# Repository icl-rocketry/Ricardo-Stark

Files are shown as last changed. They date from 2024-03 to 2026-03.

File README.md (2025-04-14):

# Ricardo-Stark (Engine Control Unit)

An integrated engine control unit designed to fire and control liquid bi-propellant rocket engines. Stark v1.0 has been tested in several cold flows and hotfire tests for engines ranging from 500N to 5kN. It has been flight tested on Nimbus 24 (ICLR's first liquid rocket launch) at the European Rocketry Challenge '24.

## Hardware (v1.0)
- ESP32-S3 microcontroller
- x2 Servo Channels with voltage monitor
- x1 Pyro Channel with regulated 12V
- x6 24 bit ADC channels
- microSD card logging
- x4 GPIO breakout
- CAN Bus
- USB-C Port

## Software (v1.0)
- Finite State Machine implementation
- Custom ignition sequence with propellant feed delay
- Custom valve angle configuration
- Optional remote configurability to ignition sequence

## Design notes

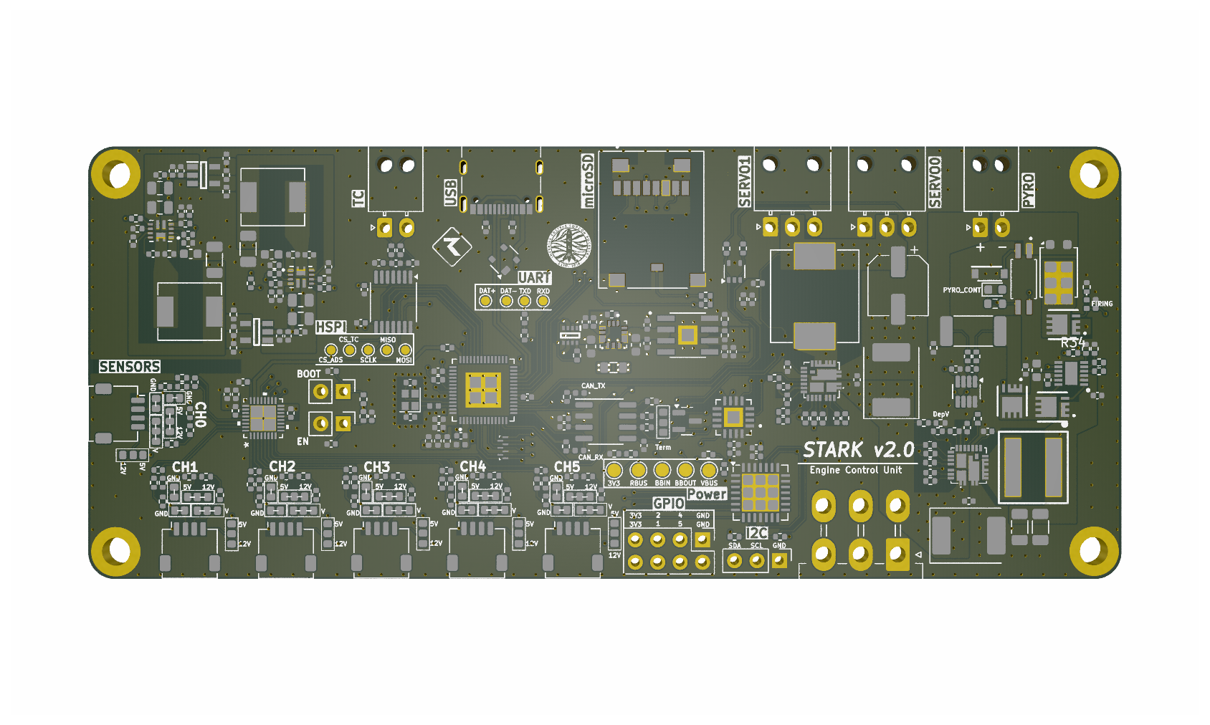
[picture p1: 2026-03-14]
Hardware/Ricardo-Stark.png

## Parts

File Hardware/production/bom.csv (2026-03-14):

Designator | Footprint | Quantity | Value | LCSC Part #
12VLED1, 3V3LED6 | 0402 | 2 | RED_LED
3V3LED1, 3V3LED4, 3V3LED8 | 0402 | 3 | BLUE_LED
3V3LED10 | 0402 | 1 | PURPLE_LED
3V3LED5 | 0402 | 1 | ORANGE_LED
3V3LED7 | 0402 | 1 | YELLOW_LED
BOOTJUMPER1, ENJUMPER1 | PinHeader_1x02_P2.54mm_Vertical | 2 | Conn_01x02_Male
C1, C15, C17, C21, C23, C31, C36, C58, C68 | 0402 | 9 | 10uF
C10, C11, C24, C3, C30, C35, C45, C5, C6, C71, C72, C76, C77, C8, C80, C84, C86, C87, C88, C89 | 0402 | 20 | 0.1uF
C12, C13 | 0402 | 2 | 11pF
C14, C32, C34, C54, C56, C59, C66, C67, C69, C83, C90 | 0402 | 11 | 100nF
C16 | 0402 | 1 | 47nF
C18, C61 | 0603 | 2 | 10uF
C19, C2, C25, C37, C4, C51, C60, C7, C73, C82 | 0402 | 10 | 1uF
C20 | 0603 | 1 | 22uF
C22, C26, C74 | 0402 | 3 | 4.7uF
C27, C28 | CP_EIA-7360-38_Kemet-E | 2 | 100uF
C29 | CP_Elec_6.3x7.7 | 1 | 470uF
C33, C38, C41, C42, C43, C44, C9 | 0402 | 7 | 10nF
C39, C52, C53, C64 | 0805 | 4 | 22uF
C40, C57, C75 | 1206 | 3 | 47uF
C46 | 0402 | 1 | 1uF | GRT188R61H225KE13D
C47 | 0603 | 1 | 0.1uF
C48 | 0603 | 1 | 2.2uF
C49 | 0402 | 1 | 180pF
C50 | 0402 | 1 | 3.9nF
C55, C65 | 0402 | 2 | 2.2uF
C62 | 0402 | 1 | 120pF
C63 | 0402 | 1 | 2.2nF
C70 | 1206 | 1 | 22uF
C78 | 0603 | 1 | 160pF
C79, C85 | 0402 | 2 | 0.01uF
C81 | 0402 | 1 | 220nF
CANRXLED1 | 0402 | 1 | CANRXLED
CANTXLED1 | 0402 | 1 | CANTXLED
D1 | SOT-23 | 1 | SM712_SOT23
D2 | SOT-143 | 1 | SP0503BAHT
D3 | TO-277B | 1 | DST1550S
D4 | 0603 | 1 | RED_LED
D6 | SOT-353_SC-70-5 | 1 | ~
D7 | RCLAMP3346PQTNT | 1 | RCLAMP3346PQTNT
D9 | SODFL3516X70N | 1 | S-102T
FIRING1 | 0402 | 1 | EMERALD_LED
H1, H2, H3, H4 | MountingHole_3.2mm_M3_DIN965_Pad | 4 | MountingHole_Pad
IC1, IC4 | IC_TPS61089RNRR | 2 | TPS61089RNRR
IC2, IC3 | SOT95P282X145-5N | 2 | AP2205-W5-7
J1 | Molex_Mini-Fit_Jr_5569-06A2_2x03_P4.20mm_Horizontal | 1 | RBUS
J10, J4, J6, J7, J8, J9 | Molex_Pico-Clasp_202396-0407_1x04-1MP_P1.00mm_Horizontal | 6 | 1053131104
J11 | PinHeader_2x04_P2.54mm_Vertical | 1 | Conn_01x08_Socket
J12 | Molex_Nano-Fit_105313-xx02_1x02_P2.50mm_Horizontal | 1 | Conn_01x02_Male
J16 | Molex_Pico-Clasp_202396-0707_1x07-1MP_P1.00mm_Horizontal | 1 | Conn_01x07_Socket
J17 | Molex_Nano-Fit_105313-xx03_1x03_P2.50mm_Horizontal | 1 | ServoCH1
J18 | Molex_Nano-Fit_105313-xx03_1x03_P2.50mm_Horizontal | 1 | ServoCH2
J2 | USB_C_Receptacle_Palconn_UTC16-G | 1 | USB_C_Receptacle_USB2.0
J3 | JAE_ST1W008S4TR2000 | 1 | ST1W008S4TR2000
J5 | PinHeader_1x03_P2.54mm_Vertical | 1 | Conn_01x03_Socket
JP10, JP12, JP13, JP14, JP17, JP18, JP19, JP20, JP23, JP24, JP25, JP28, JP29, JP3, JP30, JP33, JP5, JP6, JP7 | small_3pin_SolderJP | 19 | SolderJumper_3_Open
JP11, JP15, JP16, JP21, JP22, JP26, JP27, JP31, JP32, JP4, JP8, JP9 | SmallerSolderJP | 12 | SolderJumper_2_Open
L1 | 0402 | 1 | 2.0nH
L2 | 0402 | 1 | 20nH
L3 | 0805 | 1 | 1uH
L4 | IND_SPM10065VT-3R3M-D | 1 | 3.3uH
L5, L6 | IND_SRP6540-390M | 2 | SRR6038-5R0Y
L7 | WE-XHMI_7070 | 1 | 3.3uH
Q5, Q6, Q7 | BSZ025N04LS | 3 | BSZ025N04LS
R1, R10, R101, R13, R14, R21, R24, R25, R27, R30, R33, R38, R5, R50, R56, R76, R81, R83, R88, R9, R95 | 0402 | 21 | 10K
R100, R22, R37, R48, R55, R75, R92 | 0402 | 7 | 14k
R102, R103, R2, R3, R39, R40, R46, R47, R51, R52, R57, R58, R96, R97 | 0402 | 14 | 1k
R104, R41, R49, R53, R59, R98 | 0402 | 6 | 49
R105, R106 | 0402 | 2 | 2.2k
R107 | 0402 | 1 | 432k
R109, R110 | 0402 | 2 | 165R
R11, R94 | 0402 | 2 | 4.7k
R111, R112 | 0402 | 2 | 100
R12, R4, R43, R6 | 0402 | 4 | 470
R15 | 0402 | 1 | 0
R16, R17 | 0402 | 2 | 60.4
R18, R19, R20, R71 | 0402 | 4 | 5.1k
R23 | 0402 | 1 | 56k
R26 | 0402 | 1 | 130k
R28, R84 | 0402 | 2 | 2.2
R29 | 0402 | 1 | 294k
R31 | 0402 | 1 | 499k
R32, R44, R62, R69, R87 | 0402 | 5 | 100k
R36, R45, R54, R74, R78, R99 | 0402 | 6 | 75k
R42 | 0402 | 1 | 1.5k
R60 | 0402 | 1 | 7.87k
R61 | 0402 | 1 | 360k
R63 | 0402 | 1 | 560k
R64, R70 | 0402 | 2 | 49.9k
R65 | 0402 | 1 | 150k
R66 | 0402 | 1 | 301k
R67 | 0402 | 1 | 18.7k
R68 | 0402 | 1 | 976k
R7 | 0402 | 1 | 499R
R72 | 0402 | 1 | 475k
R73 | 0402 | 1 | 287k
R77 | 0402 | 1 | 120
R79 | 0603 | 1 | 120
R8 | 0402 | 1 | 3k
R80 | 0402 | 1 | 4.22k
R82 | 0402 | 1 | 190k
R85 | 2512 | 1 | 2m | WSLF25122L000FEB
R86 | 0402 | 1 | 200k
R89, R93 | 0402 | 2 | 10
R90 | 0603 | 1 | 5.1
R91 | 0402 | 1 | 54.9R
TC1 | Molex_Nano-Fit_105313-xx02_1x02_P2.50mm_Horizontal | 1 | Thermocouple
TP1, TP13, TP14, TP15, TP16, TP17, TP2, TP3, TP4 | TestPoint_Pad_D1.0mm | 9 | TestPoint
TP11, TP5, TP6, TP7, TP8 | TestPoint_Pad_D1.5mm | 5 | TestPoint
TXLED1 | 0402 | 1 | GREEN_LED
U1 | QFN40P700X700X90-57N | 1 | ESP32-S3
U10 | SiC437BEDT1GE3 | 1 | SiC438BED-T1-GE3
U11 | SON50P300X300X80-13N-D | 1 | LM74810
U12 | SOT-23-8 | 1 | INA219AxDCN
U13 | TSSOP-14_4.4x5mm_P0.65mm | 1 | MAX31856
U14 | QFN65P400X400X100-17N | 1 | PCA9534RGVR
U2 | SOIC-8_3.9x4.9mm_P1.27mm | 1 | SN65HVD230
U3 | SOTFL50P160X60-8N | 1 | LM66200DRLR
U4 | CONV_MAX77827AEFD+T | 1 | MAX77827AEFD+T
U5 | SOIC127P599X175-9N | 1 | SC4215
U6 | SiC437BEDT1GE3 | 1 | SiC437BED-T1-GE3
U7 | ADS131M06IRSNR | 1 | ADS131M06IPBS
U8 | QFN-28-1EP_6x6mm_P0.65mm_EP4.25x4.25mm | 1 | PCA9685BS
U9 | TCMT1109-4N | 1 | 782-TCMT1109
USBLED1 | 0402 | 1 | WHITE_LED
Y1 | Crystal_SMD_2016-4Pin_2.0x1.6mm | 1 | R940000171

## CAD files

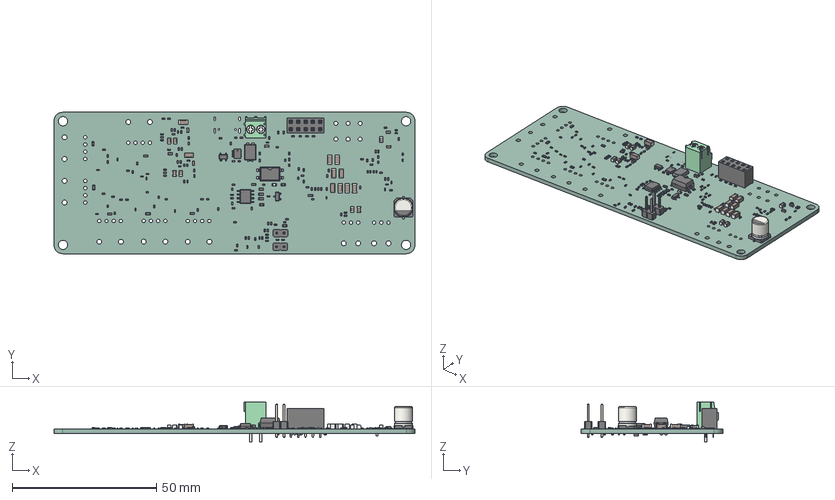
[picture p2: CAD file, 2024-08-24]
Hardware/Ricardo-Stark.step
125.0 x 49.0 x 13.7 mm
R_0402_1005Metric x 95
LED_0402_1005Metric x 12
R_0603_1608Metric x 16
C_0805_2012Metric x 6
C_0603_1608Metric x 6
C_0402_1005Metric x 54
SOIC_8_39x49mm_P127mm
L_0402_1005Metric x 2
PinHeader_1x02_P254mm_Vertical x 2
C_1206_3216Metric x 10
SMDIP_4_W953mm
TerminalBlock_Phoenix_PT_15_2_35_H_1x02_P350mm_Horizontal
SOT_143
TO_277B_sp
SOT-1210_LFPAK33
PinSocket_2x05_P254mm_Vertical
SOT_23
LED_0603_1608Metric
L_0805_2012Metric
CP_Elec_63x77
Ricardo-Stark_PCB

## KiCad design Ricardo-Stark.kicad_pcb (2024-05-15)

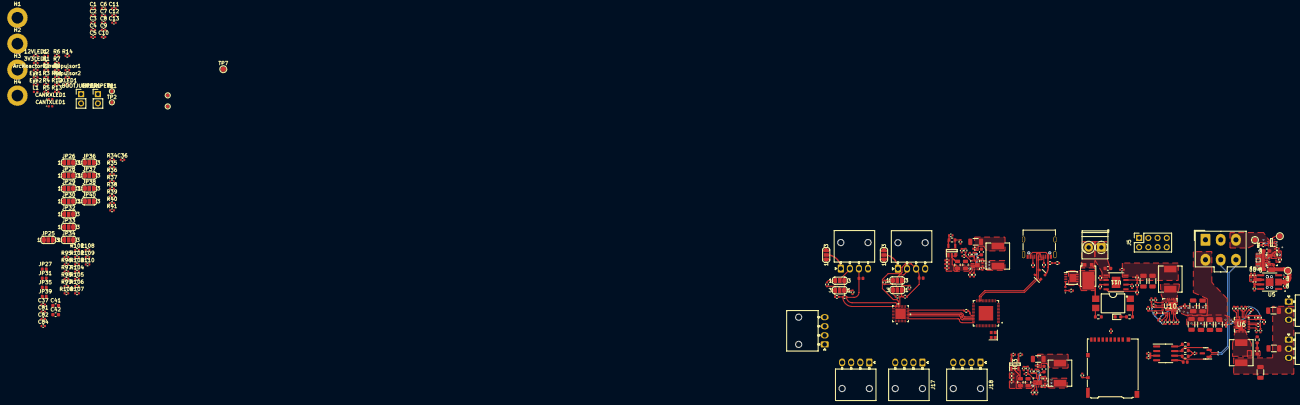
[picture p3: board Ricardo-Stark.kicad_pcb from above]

Board: 4 copper layers, 265 parts (0 on the bottom side), 164 nets.

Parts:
3V3LED1: BLUE_LED; R_0402_1005Metric
12VLED1: RED_LED; R_0402_1005Metric
ArcReactorCore1: Blue_LED; R_0402_1005Metric
BOOTJUMPER1: Conn_01x02_Male; PinHeader_1x02_P2.54mm_Vertical
C1, C15, C17, C21, C23, C58, C68: 10uF; C_0402_1005Metric
C2, C4, C7, C19, C25, C37, C51, C60, C73, C82: 1uF; C_0402_1005Metric
C3, C5, C6, C8, C10, C11, C24, C35, C36, C76, C77, C84: 0.1uF; C_0402_1005Metric
C9: 10nF; C_0402_1005Metric
C12, C13: 11pF; C_0402_1005Metric
C14, C34, C54, C56, C59, C66, C67, C69, C83, C86: 100nF; C_0402_1005Metric
C16: 47nF; C_0402_1005Metric
C18, C41, C61: 10uF; C_0603_1608Metric
C20: 22uF; C_0603_1608Metric
C22, C26, C74: 4.7uF; C_0402_1005Metric
C27, C28, C40, C57, C75, C80, C85: 47uF; C_1206_3216Metric
C29: 68uF; C_1206_3216Metric
C30, C32: DNP; C_1206_3216Metric
C31, C33: 220uF; C_1206_3216Metric
C39, C52, C53, C64: 22uF; C_0805_2012Metric
C42: 100nF; C_0603_1608Metric
C48: 2.2uF; C_0603_1608Metric
C49: 180pF; C_0402_1005Metric
C50: 3.9nF; C_0402_1005Metric
C55, C65: 2.2uF; C_0402_1005Metric
C62: 120pF; C_0402_1005Metric
C63, C87: 2.2nF; C_0402_1005Metric
C70: 22uF; C_1206_3216Metric
C78: 680pF; C_0603_1608Metric
C81: 220nF; C_0402_1005Metric
C88: 1uF; C_0603_1608Metric
CANRXLED1: CANRXLED; LED_0402_1005Metric
CANTXLED1: CANTXLED; LED_0402_1005Metric
D1: SM712_SOT23; SOT-23
D2: SP0503BAHT; SOT-143
D3: DST1550S; TO-277B
D4: RED_LED; LED_0603_1608Metric
ENJUMPER1: Conn_01x02_Male; PinHeader_1x02_P2.54mm_Vertical
Eye1, Eye2: Blue_LED; R_0402_1005Metric
Firing1: EMERALD_LED; LED_0402_1005Metric
H1, H2, H3, H4: MountingHole_Pad; MountingHole_3.2mm_M3_DIN965_Pad
IC1, IC4: TPS61089RNRR; IC_TPS61089RNRR
IC2, IC3: AP2205-W5-7; SOT95P282X145-5N
J1: RBUS; Molex_Mini-Fit_Jr_5566-06A_2x03_P4.20mm_Vertical
J2: USB_C_Receptacle_USB2.0; USB_C_Receptacle_Palconn_UTC16-G
J3: ServoCH1; Molex_Nano-Fit_105313-xx03_1x03_P2.50mm_Horizontal
J4: ServoCH2; Molex_Nano-Fit_105313-xx03_1x03_P2.50mm_Horizontal
J5: GPIO Breakout; PinSocket_2x04_P2.54mm_Vertical
J7, J14, J15, J16, J17, J18: 1053131104; Molex_Nano-Fit_105313-xx04_1x04_P2.50mm_Horizontal
J12: Conn_01x02_Male; TerminalBlock_Phoenix_PT-1,5-2-3.5-H_1x02_P3.50mm_Horizontal
J13: Micro_SD_Card_Det; microSD_HC_Hirose_DM3AT-SF-PEJM5
JP1: TermJP; SmallerSolderJP
JP5, JP10, JP20, JP21, JP22, JP24, JP25, JP26, JP28, JP29, JP30, JP32, JP33, JP34, JP36, JP37, JP38, JP40: SolderJumper_3_Open; SolderJumper-3_P1.3mm_Open_RoundedPad1.0x1.5mm_NumberLabels
JP8, JP23, JP27, JP31, JP35, JP39: SolderJumper_2_Open; SmallerSolderJP
L1: 2.0nH; L_0402_1005Metric
L2: 20nH; L_0402_1005Metric
L3: 1uH; L_0805_2012Metric
L4, L7: 3.3uH; IND_SRP6540-390M
L5, L6: SRR6038-5R0Y; IND_SRP6540-390M
Q2: BUK9M11-40EX; LFPAK33
R1, R5, R9, R10: 10K; R_0402_1005Metric
R2, R3, R11, R12, R13: 1k; R_0402_1005Metric
R4, R6, R35: 470; R_0402_1005Metric
R7: 499R; R_0402_1005Metric
R8, R14: 3k; R_0402_1005Metric
R15: 0; R_0603_1608Metric
R16, R17: 60; R_0603_1608Metric
R18, R19, R20: 5.1k; R_0402_1005Metric
R21, R24, R25, R27, R33, R48, R76, R81, R83, R88, R89, R96, R100, R104, R108: 10k; R_0402_1005Metric
R22: 14k; R_0402_1005Metric
R23: 56k; R_0402_1005Metric
R26: 130k; R_0402_1005Metric
R28, R84: 2.2; R_0402_1005Metric
R29: 294k; R_0402_1005Metric
R30: 464K; R_0402_1005Metric
R31, R86: 200k; R_0402_1005Metric
R32, R62, R69, R87: 100k; R_0402_1005Metric
R34: 1.5k; R_0402_1005Metric
R36, R37, R38, R39, R40, R41: DNP; R_0402_1005Metric
R45, R75, R95, R99, R103, R107: 58.4k; R_0402_1005Metric
R51, R92, R98, R102, R106, R110: 49; R_0402_1005Metric
R60: 7.87k; R_0402_1005Metric
R61: 360k; R_0402_1005Metric
R63: 560k; R_0402_1005Metric
R64: 50k; R_0402_1005Metric
R65: 152k; R_0603_1608Metric
R66: 301k; R_0402_1005Metric
R67: 18.7k; R_0402_1005Metric
R68: 900k; R_0402_1005Metric
R70: 51k; R_0402_1005Metric
R71: 33.2k; R_0402_1005Metric
R72: 475k; R_0402_1005Metric
R73: 287k; R_0402_1005Metric
R74, R78, R97, R101, R105, R109: 31.6k; R_0402_1005Metric
R77: 120; R_0402_1005Metric
R79: 120; R_0603_1608Metric
R80: 10k; R_0603_1608Metric
R82: 190k; R_0402_1005Metric
R85: 47.5k; R_0402_1005Metric
R90: 5.1; R_0603_1608Metric
R91: 54.9R; R_0402_1005Metric
R93: 453; R_0402_1005Metric
R94: 11.52; R_0402_1005Metric
Repulsor1, Repulsor2: White_LED; R_0402_1005Metric
TP1, TP2, TP3, TP4: TestPoint; TestPoint_Pad_D1.0mm
TP5, TP6, TP7, TP8: TestPoint; TestPoint_Pad_D1.5mm
TXLED1: GREEN_LED; R_0402_1005Metric
U1: ESP32-S3; QFN40P700X700X90-57N
U2: SN65HVD230; SOIC-8_3.9x4.9mm_P1.27mm
U3: LM66200DRLR; SOTFL50P160X60-8N
U4: MAX77827AEFD+T; CONV_MAX77827AEFD+T
U5: SC4215; SOIC127P599X175-9N
U6, U10: SiC437BED-T1-GE3; SiC437BEDT1GE3
U7: ADS131M06IPBS; ADS131M06IRSNR
U9: 859-LTV-247; SMDIP-4_W9.53mm
U11: TPS259621DDAT; SO-PP-DDA-8_TEX
USBLED1: WHITE_LED; R_0402_1005Metric
Y1: R940000171; Crystal_SMD_2016-4Pin_2.0x1.6mm

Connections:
+3.3V: C1.1, C4.1, C5.1, C7.1, C9.1, C10.1, C11.1, C14.1, C15.1, C23.2, C24.2, C37.1, C41.1, C42.1, C56.1, C57.1, C67.1, C70.1, C77.1, C82.1, C84.1, IC1.9 (VIN), IC4.9 (VIN), J5.5, J13.4 (VDD), L1.1, L5.1, L6.1, R1.1, R2.1, R3.1, R4.1, R5.1, R6.2, R9.2, R10.2, R11.1, R12.1, R13.1, R14.1, R23.1, R36.1, R37.1, R38.1, R39.1, R40.1, R41.1, R89.1, R94.2, TP7.1, U1.20 (VDD3P3_RTC), U1.46 (VDD3P3_CPU), U1.55 (VDDA), U1.56 (VDDA), U2.3 (VCC), U5.6 (VOUT), U7.15 (AVDD), U7.16 (SYNC/RESET), U7.26 (DVDD), U9.16
+5V: C55.1, IC2.5 (VOUT), JP10.1 (A), JP24.1 (A), JP28.1 (A), JP32.1 (A), JP36.1 (A), JP40.1 (A), R65.2
+6V: C29.1, C31.1, C33.1, C36.1, J3.2, J4.2, L4.1, R26.2, R29.2, R34.2, U6.18 (V_OUT)
+12V: C65.1, IC3.5 (VOUT), JP10.3 (B), JP24.3 (B), JP28.3 (B), JP32.3 (B), JP36.3 (B), JP40.3 (B)
/ADS_CLK: R91.1, U7.23 (XTAL1/CLKIN)
/ADS_CS0: U1.42 (GPIO37), U7.17 (CS)
/BOOT: BOOTJUMPER1.1, C8.1, R5.2, U1.5 (GPIO0/BOOT)
/Boosts/FB_5V: IC1.3 (FB), R61.1, R62.2
/Boosts/FB_12V: IC4.3 (FB), R68.1, R69.2
/Boosts/LDO5.5V_IN: C51.1, C52.1, C53.1, C58.1, C59.1, IC1.6 (VOUT), IC2.1 (VIN), IC2.3 (EN), R61.2
/Boosts/LDO12V_IN: C39.1, C60.1, C64.1, C68.1, C69.1, IC3.1 (VIN), IC3.3 (EN), IC4.6 (VOUT), R68.2
/Boosts/SW_5V: IC1.1 (FSW), R66.1
/Boosts/SW_12V: IC4.1 (FSW), R73.1
/CAN+: D1.2 (A2), J1.5, R16.1, U2.7 (CANH)
/CAN-: D1.1 (A1), J1.6, R17.2, U2.6 (CANL)
/CAN-BUS/Vref: JP1.1 (A), U2.5 (Vref)
/CAN_RX: CANRXLED1.1 (K), U1.6 (GPIO1/ADC1_CH0), U2.4 (R)
/CAN_TX: CANTXLED1.1 (K), U1.7 (GPIO2/ADC1_CH1), U2.1 (D)
/CHIP_PU: C2.1, C3.1, ENJUMPER1.1, R1.2, U1.4 (CHIP_PU/RESET)
/Cont 1: R79.1, U1.28 (SPI_CS1/GPIO26), U9.15
/Data+: D2.4 (K), J2.A6 (D+), J2.B6 (D+), TP4.1, U1.26 (GPIO20/USB_D+/ADC2_CH9)
/Data-: D2.3 (K), J2.A7 (D-), J2.B7 (D-), TP3.1, U1.25 (GPIO19/USB_D-/ADC2_CH8)
/HSPI_MISO: U1.39 (GPIO34), U7.20 (DOUT)
/HSPI_MOSI: U1.38 (GPIO33), U7.21 (DIN)
/HSPI_SCLK: U1.40 (GPIO35), U7.19 (SCLK)
/Nuke 1: Firing1.2 (A), Q2.4 (G), U1.27 (GPIO21)
/Power/BBIN: C17.1, C18.1, TP5.1, U3.2 (VOUT_1), U3.7 (VOUT_2), U4.3 (EN), U4.6 (IN)
/Power/BBOUT: C20.1, C21.1, C22.1, TP8.1, U4.11 (OUT), U4.13 (OUTS), U5.2 (EN), U5.3 (VIN)
/Power/BIAS: C19.1, U4.5 (BIAS)
/Power/FBIn: R23.2, R24.1, U5.7 (ADJ)
/Power/LX1: L3.1, U4.8 (LX1)
/Power/LX2: L3.2, U4.10 (LX2)
/Power/SEL: R22.1, U4.1 (SEL)
/Pyro/BOOT: C76.1, U10.23 (BOOT)
/Pyro/EFuse_In: C40.1, C75.1, C86.1, L7.1, R30.2, R82.2, U10.18 (V_OUT), U11.4 (IN)
/Pyro/EN: R88.1, U10.19 (EN)
/Pyro/FB: R82.1, R83.2, U10.17 (FB)
/Pyro/PHASE: R84.1, U10.24 (PHASE)
/Pyro/PyroV: C88.2, J12.1, U11.5 (OUT)
/Pyro/SW: L7.2, U10.5 (SW_1), U10.6 (SW_2), U10.7 (SW_3), U10.8 (SW_4), U10.9 (SW_5), U10.30 (SW_6)
/Pyro/VDD: C73.2, R81.1, R86.2, U10.15 (VDD)
/Pyro_IMON: R93.1, U1.24 (GPIO18/ADC2_CH7/DAC_1), U11.7 (ILM)
/RXD: TP2.1, U1.50 (U0RXD/PROG/GPIO44)
/SD1_DET: J13.10 (DET_A), R89.2, U1.23 (GPIO17/ADC2_CH6/DAC_2)
/Servo1PWM: J3.3, U1.16 (GPIO11/ADC2_CH0)
/Servo2PWM: J4.3, U1.15 (GPIO10/ADC1_CH9)
/ServoV_LOG: C36.2, R34.1, R35.2, U1.18 (GPIO13/ADC2_CH2)
/TXD: R7.1, TP1.1, TXLED1.1 (K)
/actuators/GPIO0: J5.2, R36.2
/actuators/GPIO1: J5.3, R37.2
/actuators/GPIO2: J5.4, R38.2
/actuators/GPIO3: J5.6, R39.2
/actuators/GPIO4: J5.7, R40.2
/actuators/GPIO5: J5.8, R41.2
/buckC/BOOT: C35.1, U6.23 (BOOT)
/buckC/EN: R33.1, U6.19 (EN)
/buckC/FB: R26.1, R27.2, R29.1, U6.17 (FB)
/buckC/PHASE: R28.1, U6.24 (PHASE)
/buckC/SW: C78.1, L4.2, U6.5 (SW_1), U6.6 (SW_2), U6.7 (SW_3), U6.8 (SW_4), U6.9 (SW_5), U6.30 (SW_6)
/buckC/VDD: C25.2, R25.1, R31.2, U6.15 (VDD)
/pressure_sensor/AIN0N: J7.3, JP8.2 (B), R51.2, U7.30 (AIM0N)
/pressure_sensor/AIN0P: JP5.3 (B), JP20.1 (A), R51.1, R75.2, R76.2, U7.29 (AIN0P)
/pressure_sensor/AIN1N: J14.3, JP23.2 (B), R92.2, U7.31 (AIN1N)
/pressure_sensor/AIN1P: JP21.3 (B), JP22.1 (A), R45.2, R48.2, R92.1, U7.32 (AIN1P)
/pressure_sensor/AIN2N: J15.3, JP27.2 (B), R98.2, U7.2 (AIN2N)
/pressure_sensor/AIN2P: JP25.3 (B), JP26.1 (A), R95.2, R96.2, R98.1, U7.1 (AIN2P)
/pressure_sensor/AIN3N: J16.3, JP31.2 (B), R102.2, U7.3 (AIN3N)
/pressure_sensor/AIN3P: JP29.3 (B), JP30.1 (A), R99.2, R100.2, R102.1, U7.4 (AIN3P)
/pressure_sensor/AIN4N: J17.3, JP35.2 (B), R106.2, U7.6 (AIN4N)
/pressure_sensor/AIN4P: JP33.3 (B), JP34.1 (A), R103.2, R104.2, R106.1, U7.5 (AIN4P)
/pressure_sensor/AIN5N: J18.3, JP39.2 (B), R110.2, U7.7 (AIN5N)
/pressure_sensor/AIN5P: JP37.3 (B), JP38.1 (A), R107.2, R108.2, R110.1, U7.8 (AIN5P)
DeployV: C27.1, C28.1, C30.1, C32.1, C34.1, C80.1, C83.1, C85.1, J1.4, R8.1, R33.2, R88.2, U6.1 (V_IN_1), U6.2 (V_IN_2), U6.22 (VIN_1), U6.26 (VIN_2), U10.1 (V_IN_1), U10.2 (V_IN_2), U10.22 (VIN_1), U10.26 (VIN_2)
GND: 3V3LED1.1 (K), 12VLED1.1 (K), ArcReactorCore1.1 (K), BOOTJUMPER1.2, C1.2, C2.2, C3.2, C4.2, C5.2, C6.2, C7.2, C8.2, C9.2, C10.2, C11.2, C12.2, C13.2, C14.2, C15.2, C16.2, C17.2, C18.2, C19.2, C20.2, C21.2, C22.2, C23.1, C24.1, C25.1, C26.1, C27.2, C28.2, C29.2, C30.2, C31.2, C32.2, C33.2, C34.2, C37.2, C39.2, C40.2, C41.2, C42.2, C48.2, C49.2, C50.2, C51.2, C52.2, C53.2, C55.2, C56.2, C57.2, C58.2, C59.2, C60.2, C61.2, C62.2, C63.2, C64.2, C65.2, C67.2, C68.2, C69.2, C70.2, C73.1, C74.1, C75.2, C77.2, C80.2, C81.2, C82.2, C83.2, C84.2, C85.2, C86.2, C87.1, C88.1, D1.3 (common), D2.1 (A), D4.1 (K), ENJUMPER1.2, Eye1.1 (K), Eye2.1 (K), H1.1, H2.1, H3.1, H4.1, IC1.5 (GND), IC2.2 (GND), IC3.2 (GND), IC4.5 (GND), J1.1, J1.2, J2.A1 (GND), J2.A12 (GND), J2.B1 (GND), J2.B12 (GND), J2.S1 (SHIELD), J3.1, J4.1, J5.1, J7.4, J13.6 (VSS), J13.9 (DET_B), J13.11 (SHIELD), J14.4, J15.4, J16.4, J17.4, J18.4, JP8.1 (A), JP23.1 (A), JP27.1 (A), JP31.1 (A), JP35.1 (A), JP39.1 (A), Q2.1 (S), Q2.2 (S), Q2.3 (S), R15.2, R18.2, R19.1, R22.2, R24.2, R27.1, R32.2, R35.1, R48.1, R62.1, R63.1, R64.1, R69.1, R70.1, R72.1, R76.1, R77.2, R80.2, R83.1, R85.2, R87.2, R90.2, R93.2, R96.1, R100.1, R104.1, R108.1, Repulsor1.1 (K), Repulsor2.1 (K), U1.57 (GND), U2.2 (GND), U3.1 (GND_1), U3.4 (~ON), U3.5 (GND_2), U4.4 (AGND), U4.9 (PGND), U5.8 (GND), U5.9 (GND), U6.3 (P_GND_1), U6.4 (P_GND_2), U6.13 (P_GND_3), U6.16 (A_GND), U6.25 (AGND), U6.27 (PGND), U6.29 (P_GND_4), U7.13 (AGND), U7.22 (XTAL2), U7.25 (DGND), U7.28 (AGND), U10.3 (P_GND_1), U10.4 (P_GND_2), U10.13 (P_GND_3), U10.16 (A_GND), U10.25 (AGND), U10.27 (PGND), U10.29 (P_GND_4), U11.1 (GND), U11.EPAD (GND), USBLED1.1 (K), Y1.2, Y1.4
unnamed: 3V3LED1.2 (A), R6.1
unnamed: 12VLED1.2 (A), R8.2
unnamed: ArcReactorCore1.2 (A), R11.2
unnamed: C6.1, L1.2, U1.2 (VDD3P3), U1.3 (VDD3P3)
unnamed: C13.1, L2.2, Y1.1
unnamed: C35.2, R28.2
unnamed: C50.1, R60.2
unnamed: C63.1, R67.2
unnamed: C76.2, R84.2
unnamed: C78.2, R90.1
unnamed: CANRXLED1.2 (A), R3.2
unnamed: CANTXLED1.2 (A), R2.2
unnamed: D3.3 (K), Q2.5 (D)
unnamed: D4.2 (A), R79.2
unnamed: Eye1.2 (A), Eye2.2 (A), R14.2
unnamed: Firing1.1 (K), R77.1
unnamed: C54.1, IC1.10 (BOOT)
unnamed: C49.1, IC1.4 (COMP), R60.1
unnamed: IC1.7 (EN), R9.1
unnamed: IC1.8 (ILIM), R63.2
unnamed: C54.2, IC1.11 (SW), L5.2, R66.2
unnamed: C48.1, IC1.2 (VCC)
unnamed: IC2.4 (ADJ/NC), R64.2, R65.1
unnamed: IC3.4 (ADJ/NC), R70.2
unnamed: C66.1, IC4.10 (BOOT)
unnamed: C62.1, IC4.4 (COMP), R67.1
unnamed: IC4.7 (EN), R10.1
unnamed: IC4.8 (ILIM), R72.2
unnamed: C66.2, IC4.11 (SW), L6.2, R73.2
unnamed: C61.1, IC4.2 (VCC)
unnamed: J2.A5 (CC1), R18.1
unnamed: J2.B5 (CC2), R19.2
unnamed: D3.1 (A), D3.2 (A), J12.2, U9.1
unnamed: C16.1, JP1.2 (B), R16.2, R17.1
unnamed: JP5.1 (A), R74.1
unnamed: J7.2, JP5.2 (C)
unnamed: J7.1, JP10.2 (C)
unnamed: JP20.3 (B), R75.1
unnamed: JP20.2 (C), R74.2
unnamed: JP21.1 (A), R78.1
unnamed: J14.2, JP21.2 (C)
unnamed: JP22.3 (B), R45.1
unnamed: JP22.2 (C), R78.2
unnamed: J14.1, JP24.2 (C)
unnamed: JP25.1 (A), R97.1
unnamed: J15.2, JP25.2 (C)
unnamed: JP26.3 (B), R95.1
unnamed: JP26.2 (C), R97.2
unnamed: J15.1, JP28.2 (C)
unnamed: JP29.1 (A), R101.1
unnamed: J16.2, JP29.2 (C)
unnamed: JP30.3 (B), R99.1
unnamed: JP30.2 (C), R101.2
unnamed: J16.1, JP32.2 (C)
unnamed: JP33.1 (A), R105.1
unnamed: J17.2, JP33.2 (C)
unnamed: JP34.3 (B), R103.1
unnamed: JP34.2 (C), R105.2
unnamed: J17.1, JP36.2 (C)
unnamed: JP37.1 (A), R109.1
unnamed: J18.2, JP37.2 (C)
unnamed: JP38.3 (B), R107.1
unnamed: JP38.2 (C), R109.2
unnamed: J18.1, JP40.2 (C)
unnamed: R80.1, U9.2
unnamed: R12.2, Repulsor1.2 (A)
unnamed: R13.2, Repulsor2.2 (A)
unnamed: R4.2, TXLED1.2 (A)
unnamed: R91.2, U1.37 (SPICLK_P/GPIO47)
unnamed: R7.2, U1.49 (U0TXD/PROG/GPIO43)
unnamed: C12.1, U1.53 (XTAL_N), Y1.3
unnamed: L2.1, U1.54 (XTAL_P)
unnamed: R15.1, U2.8 (Rs)
unnamed: R21.2, U3.8 (ST)
unnamed: R31.1, U6.20 (MODE_2)
unnamed: R25.2, U6.14 (P_GOOD)
unnamed: C26.2, U6.12 (V_DRV)
unnamed: R32.1, U6.21 (_MODE_1)
unnamed: C81.1, U7.24 (CAP)
unnamed: R86.1, U10.20 (MODE_2)
unnamed: R81.2, U10.14 (P_GOOD)
unnamed: C74.2, U10.12 (V_DRV)
unnamed: R87.1, U10.21 (_MODE_1)
unnamed: R94.1, U11.6 (*FLT)
unnamed: R30.1, R71.2, U11.3 (EN/UVLO)
unnamed: R71.1, R85.1, U11.8 (OVLO/OVCSEL)
unnamed: C87.2, U11.2 (dVdt)
unnamed: R20.2, USBLED1.2 (A)
RBUS_uC_V: J1.3, TP6.1, U3.6 (VIN2)
VBUS: D2.2 (K), J2.A4 (VBUS), J2.A9 (VBUS), J2.B4 (VBUS), J2.B9 (VBUS), R20.1, R21.1, U3.3 (VIN1)

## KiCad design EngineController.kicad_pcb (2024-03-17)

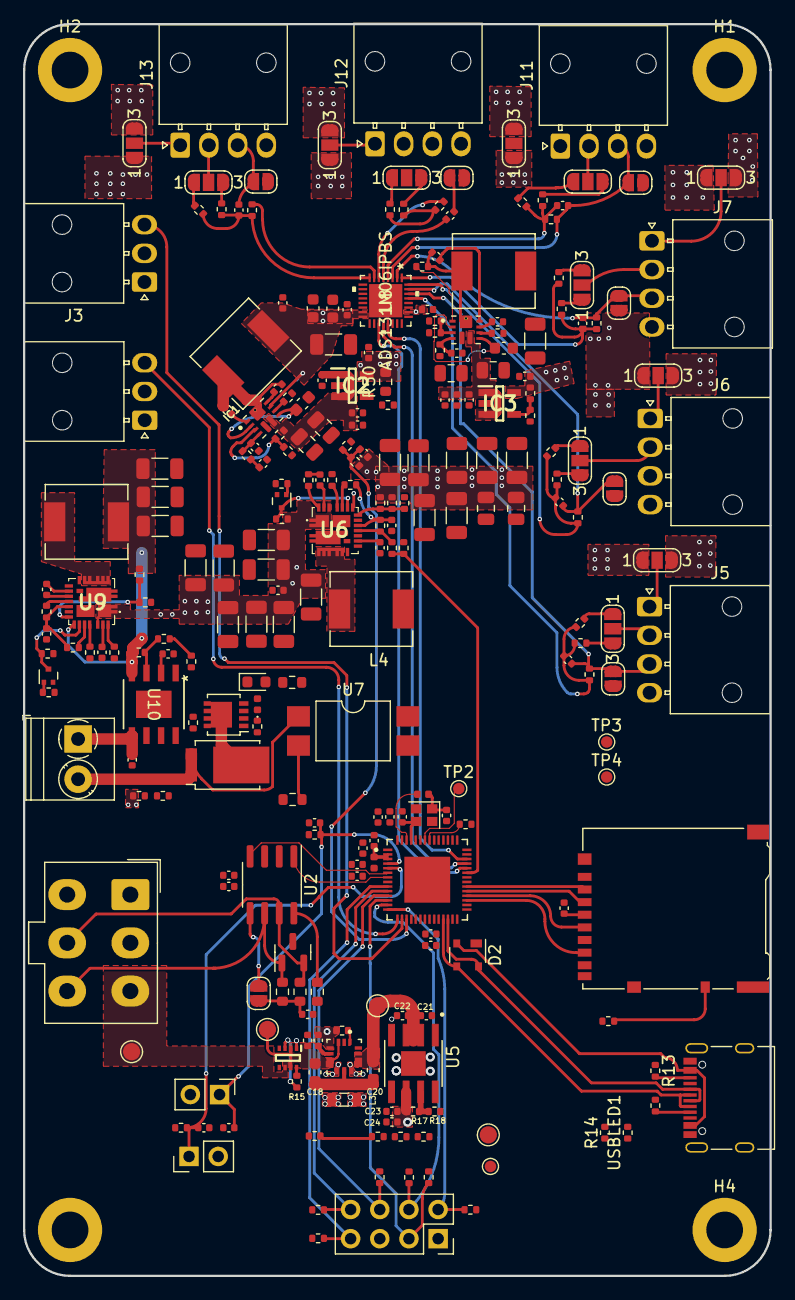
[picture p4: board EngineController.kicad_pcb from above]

Board: 4 copper layers, 65.0 x 109.0 mm, 251 parts (0 on the bottom side), 150 nets.

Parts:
3V3LED1: BLUE_LED; R_0402_1005Metric
12VLED1: RED_LED; R_0402_1005Metric
BOOTJUMPER1: Conn_01x02_Male; PinHeader_1x02_P2.54mm_Vertical
C1, C15, C17, C21, C23, C66, C74: 10uF; C_0402_1005Metric
C2, C4, C7, C19, C25, C59, C68, C69, C71, C72: 1uF; C_0402_1005Metric
C3, C5, C6, C8, C10, C11, C24, C35, C46, C47, C91: 0.1uF; C_0402_1005Metric
C9, C48, C50, C51, C53, C54, C55: 10nF; C_0402_1005Metric
C12, C13: 11pF; C_0402_1005Metric
C14, C34, C62, C64, C67, C75, C80, C81: 100nF; C_0402_1005Metric
C16: 47nF; C_0402_1005Metric
C18, C49, C76: 10uF; C_0603_1608Metric
C20: 22uF; C_0603_1608Metric
C22, C26, C70: 4.7uF; C_0402_1005Metric
C27, C28, C29, C31, C33, C65, C85, C87, C89: 47uF; C_1206_3216Metric
C30, C32, C36, C38, C39, C40, C42, C43, C44, C45: DNP; C_1206_3216Metric
C37, C41: DNP; C_0805_2012Metric
C52: 100nF; C_0603_1608Metric
C56: 2.2uF; C_0603_1608Metric
C57: 180pF; C_0402_1005Metric
C58: 4.7nF; C_0402_1005Metric
C60, C61, C79: 22uF; C_0805_2012Metric
C63, C73: 2.2uF; C_0402_1005Metric
C77: 120pF; C_0402_1005Metric
C78: 2.2nF; C_0805_2012Metric
C82: 22uF; C_1206_3216Metric
C92: 2.2nF; C_0402_1005Metric
C93: 100uF; C_0402_1005Metric
D1: SM712_SOT23; SOT-23
D2: SP0503BAHT; SOT-143
D4: DST1550S; TO-277B
D6: RED_LED; LED_0603_1608Metric
ENJUMPER1: Conn_01x02_Male; PinHeader_1x02_P2.54mm_Vertical
Firing1: EMERALD_LED; LED_0402_1005Metric
H1, H2, H3, H4: MountingHole_Pad; MountingHole_3.2mm_M3_DIN965_Pad
IC1, IC4: TPS61089RNRR; IC_TPS61089RNRR
IC2, IC3: AP2205-W5-7; SOT95P282X145-5N
J1: RBUS; Molex_Mini-Fit_Jr_5566-06A_2x03_P4.20mm_Vertical
J2: USB_C_Receptacle_USB2.0; USB_C_Receptacle_Palconn_UTC16-G
J3: ServoCH1; Molex_Nano-Fit_105313-xx03_1x03_P2.50mm_Horizontal
J4: ServoCH2; Molex_Nano-Fit_105313-xx03_1x03_P2.50mm_Horizontal
J5, J6, J7, J11, J12, J13: 1053131104; Molex_Nano-Fit_105313-xx04_1x04_P2.50mm_Horizontal
J8: GPIO Breakout; PinSocket_2x04_P2.54mm_Vertical
J9: Micro_SD_Card_Det; microSD_HC_Hirose_DM3AT-SF-PEJM5
J10: Conn_01x02_Male; TerminalBlock_Phoenix_PT-1,5-2-3.5-H_1x02_P3.50mm_Horizontal
JP1: TermJP; SolderJumper-2_P1.3mm_Open_RoundedPad1.0x1.5mm
JP2, JP4, JP5, JP7, JP8, JP10, JP11, JP13, JP14, JP16, JP17, JP19: SolderJumper_3_Open; SolderJumper-3_P1.3mm_Open_RoundedPad1.0x1.5mm_NumberLabels
JP3, JP6, JP9, JP12, JP15, JP18: SolderJumper_2_Open; SolderJumper-2_P1.3mm_Open_RoundedPad1.0x1.5mm
L1: 2.0nH; L_0402_1005Metric
L2: 20nH; L_0402_1005Metric
L3: 1uH; L_0805_2012Metric
L4, L7: 3.3uH; IND_SRP6540-390M
L5, L6: SRR6038-5R0Y; IND_SRP6540-390M
Q1, Q3: SSM3K15AMFV,L3F; SOT-723
Q2: BUK9M11-40EX; LFPAK33
R1, R3: 10K; R_0402_1005Metric
R2, R4, R29: 470; R_0402_1005Metric
R5: 499R; R_0402_1005Metric
R6: 3k; R_0402_1005Metric
R7, R28: 1.5k; R_0402_1005Metric
R8: 2.2k; R_0402_1005Metric
R9: 0; R_0603_1608Metric
R10, R11: 60; R_0603_1608Metric
R12, R13, R14: 5.1k; R_0402_1005Metric
R15, R18, R19, R21, R27, R32, R35, R38, R41, R44, R47, R54, R57, R66, R67, R75, R86: 10k; R_0402_1005Metric
R16: 14k; R_0402_1005Metric
R17: 56k; R_0402_1005Metric
R20: 130k; R_0402_1005Metric
R22, R69: 2.2; R_0402_1005Metric
R23: 294k; R_0402_1005Metric
R24, R72: 1k; R_0402_1005Metric
R25, R73: 200k; R_0402_1005Metric
R26, R74: 100k; R_0402_1005Metric
R30, R33, R36, R39, R42, R52: 90k; R_0402_1005Metric
R31, R34, R37, R40, R43, R53: 31.7k; R_0402_1005Metric
R45: 17.4k; R_0402_1005Metric
R46: 1K; R_0402_1005Metric
R48: 127k; R_0402_1005Metric
R49: 50k; R_0402_1005Metric
R50: 152k; R_0603_1608Metric
R51: 301k; R_0402_1005Metric
R55: 51k; R_0402_1005Metric
R56: 0k; R_0402_1005Metric
R58: 190k; R_0402_1005Metric
R59, R60, R61, R62, R63, R64: DNP; R_0402_1005Metric
R65: 120; R_0402_1005Metric
R68: 120; R_0603_1608Metric
R70: 10k; R_0603_1608Metric
R76: 464K; R_0402_1005Metric
R77: 33.2K; R_0402_1005Metric
R78: 47.5K; R_0402_1005Metric
R79: 453; R_0402_1005Metric
R84: 18.7k; R_0402_1005Metric
R85: 2k; R_0402_1005Metric
R87: 475k; R_0402_1005Metric
R88: 287k; R_0402_1005Metric
TP1, TP2, TP3, TP4: TestPoint; TestPoint_Pad_D1.0mm
TP5, TP6, TP7, TP8: TestPoint; TestPoint_Pad_D1.5mm
TXLED1: GREEN_LED; R_0402_1005Metric
U1: ESP32-S3; QFN40P700X700X90-57N
U2: SN65HVD230; SOIC-8_3.9x4.9mm_P1.27mm
U3: LM66200DRLR; SOTFL50P160X60-8N
U4: MAX77827AEFD+T; CONV_MAX77827AEFD+T
U5: SC4215; SOIC127P599X175-9N
U6, U9: SiC437BED-T1-GE3; SiC437BEDT1GE3
U7: LTV-247; SMDIP-4_W9.53mm
U8: ADS131M06IPBS; ADS131M06IRSNR
U10: TPS259621DDAT; SO-PP-DDA-8_TEX
USBLED1: WHITE_LED; R_0402_1005Metric
Y1: R940000171; Crystal_SMD_2016-4Pin_2.0x1.6mm

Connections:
+3.3V: C1.1, C4.1, C5.1, C7.1, C9.1, C10.1, C11.1, C14.1, C15.1, C23.2, C24.2, C47.1, C49.1, C52.1, C64.1, C65.1, C71.1, C72.2, C81.1, C82.1, IC1.9 (VIN), IC4.9 (VIN), J8.5, J9.4 (VDD), L1.1, L5.1, L6.1, R1.1, R2.1, R3.1, R4.2, R17.1, R59.1, R60.1, R61.1, R62.1, R63.1, R64.1, R66.1, TP7.1, U1.20 (VDD3P3_RTC), U1.46 (VDD3P3_CPU), U1.55 (VDDA), U1.56 (VDDA), U2.3 (VCC), U5.6 (VOUT), U7.16, U8.15 (AVDD), U8.16 (SYNC/RESET), U8.26 (DVDD)
+5V: C63.1, IC2.5 (VOUT), JP4.1 (A), JP7.1 (A), JP10.1 (A), JP13.1 (A), JP16.1 (A), JP19.1 (A), R50.2
+6V: C29.1, C31.1, C33.1, C37.1, C39.1, C41.1, C43.1, C44.1, C45.1, C46.1, J3.2, J4.2, L4.1, R20.2, R23.2, R28.2, U6.18 (V_OUT)
+12V: C27.1, C28.1, C30.1, C32.1, C34.1, C36.1, C38.1, C40.1, C42.1, C73.1, IC3.5 (VOUT), J1.4, JP4.3 (B), JP7.3 (B), JP10.3 (B), JP13.3 (B), JP16.3 (B), JP19.3 (B), R6.1, R27.2, R56.2, U6.1 (V_IN_1), U6.2 (V_IN_2), U6.22 (VIN_1), U6.26 (VIN_2), U9.1 (V_IN_1), U9.2 (V_IN_2), U9.22 (VIN_1), U9.26 (VIN_2)
/ADS_CLK: U1.24 (GPIO18/ADC2_CH7/DAC_1), U8.23 (XTAL1/CLKIN)
/ADS_CS0: U1.27 (GPIO21), U8.17 (CS)
/BOOT: BOOTJUMPER1.1, C8.1, R3.2, U1.5 (GPIO0/BOOT)
/Boosts/FB_5V: IC1.3 (FB), R46.1, R47.2
/Boosts/FB_10V: IC4.3 (FB), R85.1, R86.2
/Boosts/LDO5.5V_IN: C59.1, C60.1, C61.1, C66.1, C67.1, IC1.6 (VOUT), IC2.1 (VIN), IC2.3 (EN), R46.2
/Boosts/LDO12V_IN: C69.1, C74.1, C75.1, C79.1, IC3.1 (VIN), IC3.3 (EN), IC4.6 (VOUT), R85.2
/Boosts/SW_5V: IC1.1 (FSW), R51.1
/Boosts/SW_10V: IC4.1 (FSW), R88.1
/BuckPGOOD: R7.1, R8.2, U1.37 (SPICLK_P/GPIO47)
/CAN+: D1.2 (A2), J1.5, R10.1, U2.7 (CANH)
/CAN-: D1.1 (A1), J1.6, R11.2, U2.6 (CANL)
/CAN-BUS/Vref: JP1.1 (A), U2.5 (Vref)
/CAN_RX: U1.6 (GPIO1/ADC1_CH0), U2.4 (R)
/CAN_TX: U1.7 (GPIO2/ADC1_CH1), U2.1 (D)
/CHIP_PU: C2.1, C3.1, ENJUMPER1.1, R1.2, U1.4 (CHIP_PU/RESET)
/Data+: D2.4 (K), J2.A6 (D+), J2.B6 (D+), TP4.1, U1.26 (GPIO20/USB_D+/ADC2_CH9)
/Data-: D2.3 (K), J2.A7 (D-), J2.B7 (D-), TP3.1, U1.25 (GPIO19/USB_D-/ADC2_CH8)
/HSPI_MISO: U1.39 (GPIO34), U8.20 (DOUT)
/HSPI_MOSI: U1.40 (GPIO35), U8.21 (DIN)
/HSPI_SCLK: U1.38 (GPIO33), U8.19 (SCLK)
/Power/BBIN: C17.1, C18.1, TP5.1, U3.2 (VOUT_1), U3.7 (VOUT_2), U4.3 (EN), U4.6 (IN)
/Power/BBOUT: C20.1, C21.1, C22.1, TP8.1, U4.11 (OUT), U4.13 (OUTS), U5.2 (EN), U5.3 (VIN)
/Power/BIAS: C19.1, U4.5 (BIAS)
/Power/FBIn: R17.2, R18.1, U5.7 (ADJ)
/Power/LX1: L3.1, U4.8 (LX1)
/Power/LX2: L3.2, U4.10 (LX2)
/Power/SEL: R16.1, U4.1 (SEL)
/Pyro/BOOT: C91.1, U9.23 (BOOT)
/Pyro/BUCKP_EN: Q3.1 (G), R72.2
/Pyro/Cont1: R68.1, U7.15
/Pyro/EFuse_In: C85.1, C87.1, C89.1, L7.1, R58.2, R76.2, U9.18 (V_OUT), U10.4 (IN)
/Pyro/EN: Q3.3 (D), R75.1, U9.19 (EN)
/Pyro/FB: R58.1, R67.2, U9.17 (FB)
/Pyro/Nuke 1: Firing1.2 (A), Q2.4 (G)
/Pyro/PGOOD: R57.2, U9.14 (P_GOOD)
/Pyro/PHASE: R69.1, U9.24 (PHASE)
/Pyro/PyroV: C93.2, J10.1, U10.5 (OUT)
/Pyro/SW: L7.2, U9.5 (SW_1), U9.6 (SW_2), U9.7 (SW_3), U9.8 (SW_4), U9.9 (SW_5), U9.30 (SW_6)
/Pyro/VDD: C68.2, R57.1, R73.2, U9.15 (VDD)
/RXD: TP2.1, U1.50 (U0RXD/PROG/GPIO44)
/Servo1PWM: J3.3, U1.16 (GPIO11/ADC2_CH0)
/Servo2PWM: J4.3, U1.15 (GPIO10/ADC1_CH9)
/ServoV_LOG: C46.2, R28.1, R29.2, U1.17 (GPIO12/ADC2_CH1)
/TXD: R5.1, TP1.1, TXLED1.1 (K)
/actuators/GPIO0: J8.2, R59.2, U1.14 (GPIO9/ADC1_CH8)
/actuators/GPIO1: J8.3, R60.2, U1.12 (GPIO7/ADC1_CH6)
/actuators/GPIO2: J8.4, R61.2, U1.13 (GPIO8/ADC1_CH7)
/actuators/GPIO3: J8.6, R62.2, U1.11 (GPIO6/ADC1_CH5)
/actuators/GPIO4: J8.7, R63.2, U1.9 (GPIO4/ADC1_CH3)
/actuators/GPIO5: J8.8, R64.2, U1.10 (GPIO5/ADC1_CH4)
/buckC/BOOT: C35.1, U6.23 (BOOT)
/buckC/BUCKC_EN: Q1.1 (G), R24.2, U1.18 (GPIO13/ADC2_CH2)
/buckC/EN: Q1.3 (D), R27.1, U6.19 (EN)
/buckC/FB: R20.1, R21.2, R23.1, U6.17 (FB)
/buckC/PGOOD: R7.2, R19.2, U6.14 (P_GOOD)
/buckC/PHASE: R22.1, U6.24 (PHASE)
/buckC/SW: L4.2, U6.5 (SW_1), U6.6 (SW_2), U6.7 (SW_3), U6.8 (SW_4), U6.9 (SW_5), U6.30 (SW_6)
/buckC/VDD: C25.2, R19.1, R25.2, U6.15 (VDD)
/microSD/SD1_DET: J9.10 (DET_A), R66.2
/microSD/VSPI_MISO: J9.7 (DAT0), U1.31 (SPIWP/GPIO28)
/microSD/VSPI_SCLK: J9.5 (CLK), U1.32 (SPICS0/GPIO29)
/pressure_sensor/AIN0N: C48.2, J5.3, JP3.2 (B), R32.2, U8.30 (AIM0N)
/pressure_sensor/AIN0P: C48.1, R30.2, R31.2, R32.1, U8.29 (AIN0P)
/pressure_sensor/AIN1N: C50.2, J6.3, JP6.2 (B), R35.2, U8.31 (AIN1N)
/pressure_sensor/AIN1P: C50.1, R33.2, R34.2, R35.1, U8.32 (AIN1P)
/pressure_sensor/AIN2N: C51.2, J7.3, JP9.2 (B), R38.2, U8.2 (AIN2N)
/pressure_sensor/AIN2P: C51.1, R36.2, R37.2, R38.1, U8.1 (AIN2P)
/pressure_sensor/AIN3N: C53.2, J11.3, JP12.2 (B), R41.2, U8.3 (AIN3N)
/pressure_sensor/AIN3P: C53.1, R39.2, R40.2, R41.1, U8.4 (AIN3P)
/pressure_sensor/AIN4N: C54.2, J12.3, JP15.2 (B), R44.2, U8.6 (AIN4N)
/pressure_sensor/AIN4P: C54.1, R42.2, R43.2, R44.1, U8.5 (AIN4P)
/pressure_sensor/AIN5N: C55.2, J13.3, JP18.2 (B), R54.2, U8.7 (AIN5N)
/pressure_sensor/AIN5P: C55.1, R52.2, R53.2, R54.1, U8.8 (AIN5P)
GND: 3V3LED1.1 (K), 12VLED1.1 (K), BOOTJUMPER1.2, C1.2, C2.2, C3.2, C4.2, C5.2, C6.2, C7.2, C8.2, C9.2, C10.2, C11.2, C12.2, C13.2, C14.2, C15.2, C16.2, C17.2, C18.2, C19.2, C20.2, C21.2, C22.2, C23.1, C24.1, C25.1, C26.1, C27.2, C28.2, C29.2, C30.2, C31.2, C32.2, C33.2, C34.2, C36.2, C37.2, C38.2, C39.2, C40.2, C41.2, C42.2, C43.2, C44.2, C45.2, C47.2, C49.2, C52.2, C56.2, C57.2, C58.2, C59.2, C60.2, C61.2, C63.2, C64.2, C65.2, C66.2, C67.2, C68.1, C69.2, C70.1, C71.2, C72.1, C73.2, C74.2, C75.2, C76.2, C77.2, C78.2, C79.2, C81.2, C82.2, C85.2, C87.2, C89.2, C92.1, C93.1, D1.3 (common), D2.1 (A), D6.1 (K), ENJUMPER1.2, H1.1, H2.1, H3.1, H4.1, IC1.5 (GND), IC2.2 (GND), IC3.2 (GND), IC4.5 (GND), J1.1, J1.2, J2.A1 (GND), J2.A12 (GND), J2.B1 (GND), J2.B12 (GND), J2.S1 (SHIELD), J3.1, J4.1, J5.4, J6.4, J7.4, J8.1, J9.6 (VSS), J9.9 (DET_B), J9.11 (SHIELD), J11.4, J12.4, J13.4, JP3.1 (A), JP6.1 (A), JP9.1 (A), JP12.1 (A), JP15.1 (A), JP18.1 (A), Q1.2 (S), Q2.1 (S), Q2.2 (S), Q2.3 (S), Q3.2 (S), R8.1, R9.2, R12.2, R13.1, R16.2, R18.2, R21.1, R24.1, R26.2, R29.1, R47.1, R48.1, R49.1, R55.1, R65.2, R67.1, R70.2, R72.1, R74.2, R78.2, R86.1, R87.1, U1.57 (GND), U2.2 (GND), U3.1 (GND_1), U3.4 (~ON), U3.5 (GND_2), U4.4 (AGND), U4.9 (PGND), U5.8 (GND), U5.9 (GND), U6.3 (P_GND_1), U6.4 (P_GND_2), U6.13 (P_GND_3), U6.16 (A_GND), U6.25 (AGND), U6.27 (PGND), U6.29 (P_GND_4), U8.13 (AGND), U8.25 (DGND), U9.3 (P_GND_1), U9.4 (P_GND_2), U9.13 (P_GND_3), U9.16 (A_GND), U9.25 (AGND), U9.27 (PGND), U9.29 (P_GND_4), U10.1 (GND), U10.EPAD (GND), USBLED1.1 (K), Y1.2, Y1.4
unnamed: 3V3LED1.2 (A), R4.1
unnamed: 12VLED1.2 (A), R6.2
unnamed: C6.1, L1.2, U1.2 (VDD3P3), U1.3 (VDD3P3)
unnamed: C13.1, L2.2, Y1.1
unnamed: C35.2, R22.2
unnamed: C58.1, R45.2
unnamed: C78.1, R84.2
unnamed: C91.2, R69.2
unnamed: D4.3 (K), Q2.5 (D)
unnamed: D6.2 (A), R68.2
unnamed: Firing1.1 (K), R65.1
unnamed: C62.1, IC1.10 (BOOT)
unnamed: C57.1, IC1.4 (COMP), R45.1
unnamed: C56.1, IC1.2 (VCC), IC1.7 (EN)
unnamed: IC1.8 (ILIM), R48.2
unnamed: C62.2, IC1.11 (SW), L5.2, R51.2
unnamed: IC2.4 (ADJ/NC), R49.2, R50.1
unnamed: IC3.4 (ADJ/NC), R55.2, R56.1
unnamed: C80.1, IC4.10 (BOOT)
unnamed: C77.1, IC4.4 (COMP), R84.1
unnamed: C76.1, IC4.2 (VCC), IC4.7 (EN)
unnamed: IC4.8 (ILIM), R87.2
unnamed: C80.2, IC4.11 (SW), L6.2, R88.2
unnamed: J2.A5 (CC1), R12.1
unnamed: J2.B5 (CC2), R13.2
unnamed: D4.1 (A), D4.2 (A), J10.2, U7.1
unnamed: C16.1, JP1.2 (B), R10.2, R11.1
unnamed: JP2.1 (A), R31.1
unnamed: JP2.3 (B), R30.1
unnamed: J5.2, JP2.2 (C)
unnamed: J5.1, JP4.2 (C)
unnamed: JP5.1 (A), R34.1
unnamed: JP5.3 (B), R33.1
unnamed: J6.2, JP5.2 (C)
unnamed: J6.1, JP7.2 (C)
unnamed: JP8.1 (A), R37.1
unnamed: JP8.3 (B), R36.1
unnamed: J7.2, JP8.2 (C)
unnamed: J7.1, JP10.2 (C)
unnamed: JP11.1 (A), R40.1
unnamed: JP11.3 (B), R39.1
unnamed: J11.2, JP11.2 (C)
unnamed: J11.1, JP13.2 (C)
unnamed: JP14.1 (A), R43.1
unnamed: JP14.3 (B), R42.1
unnamed: J12.2, JP14.2 (C)
unnamed: J12.1, JP16.2 (C)
unnamed: JP17.1 (A), R53.1
unnamed: JP17.3 (B), R52.1
unnamed: J13.2, JP17.2 (C)
unnamed: J13.1, JP19.2 (C)
unnamed: R70.1, U7.2
unnamed: R2.2, TXLED1.2 (A)
unnamed: R5.2, U1.49 (U0TXD/PROG/GPIO43)
unnamed: C12.1, U1.53 (XTAL_N), Y1.3
unnamed: L2.1, U1.54 (XTAL_P)
unnamed: R9.1, U2.8 (Rs)
unnamed: R15.2, U3.8 (ST)
unnamed: R25.1, U6.20 (MODE_2)
unnamed: C26.2, U6.12 (V_DRV)
unnamed: R26.1, U6.21 (_MODE_1)
unnamed: R73.1, U9.20 (MODE_2)
unnamed: C70.2, U9.12 (V_DRV)
unnamed: R74.1, U9.21 (_MODE_1)
unnamed: R76.1, R77.2, U10.3 (EN/UVLO)
unnamed: R79.1, U10.7 (ILM)
unnamed: R77.1, R78.1, R79.2, U10.8 (OVLO/OVCSEL)
unnamed: C92.2, U10.2 (dVdt)
unnamed: R14.2, USBLED1.2 (A)
RBUS_uC_V: J1.3, TP6.1, U3.6 (VIN2)
VBUS: D2.2 (K), J2.A4 (VBUS), J2.A9 (VBUS), J2.B4 (VBUS), J2.B9 (VBUS), R14.1, R15.1, U3.3 (VIN1)

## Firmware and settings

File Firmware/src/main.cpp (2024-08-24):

#include "freertos/FreeRTOS.h"
#include "freertos/task.h"
#include "esp_task_wdt.h"

#include <Arduino.h>
#define ARDUINO_LOOP_STACK_SIZE 8192


#include <exception>

#include "system.h"




static constexpr bool exceptionsEnabled = true; //for debugging -> will integrate this into the sd configuration options later


TaskHandle_t loopTaskHandle = NULL;

System ricSystem;


void setup_task()
{
    //MUST CALL CORE SYSTEM SETUP
    ricSystem.coreSystemSetup();
    // setup();
}

void inner_loop_task()
{
    //must call core system update
    ricSystem.coreSystemUpdate();
    // loop();
}

void loopTask(void *pvParameters)
{
    // esp_log_level_set("*", ESP_LOG_INFO); 
    setup_task();
    for(;;) {
        inner_loop_task();
        vTaskDelay(1); // this is important to allow the watchdog to be reset, and to let any other threads on the core work
    }
}

extern "C" void app_main()
{
    initArduino(); //probably dont even need this
    xTaskCreateUniversal(loopTask, "loopTask", ARDUINO_LOOP_STACK_SIZE, NULL, 1, &loopTaskHandle, 1);
}

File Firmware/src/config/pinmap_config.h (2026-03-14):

/*
**********************
* PINS               *
**********************
 */
#pragma once
#include <stdint.h>

// v2 Pins

namespace PinMap{

    
    // CAN
    static constexpr uint8_t RxCan = 10; 
    static constexpr uint8_t TxCan = 11; 
    
    // SD
    static constexpr uint8_t SdDet = 39; //change
    static constexpr uint8_t SdCs = 18;
    static constexpr uint8_t V_MOSI = 17;
    static constexpr uint8_t V_SCLK = 16;
    static constexpr uint8_t V_MISO = 15;

    // Servo
    static constexpr uint8_t ServoPWM1 = 14; 
    static constexpr uint8_t ServoPWM2 = 13; 
    static constexpr uint8_t ServoVLog = 8; 

    // Pyro
    static constexpr uint8_t PyroCont = 3; //NB this is on the pyro pin expander
    static constexpr uint8_t PyroNuke = 9;
    static constexpr uint8_t PyroPowerSwitch = 1; //NB this is on the pyro pin expander

    // LED
    // static constexpr uint8_t LED = 26; //chnage

    // Sensors
    static constexpr uint8_t H_MISO = 33;
    static constexpr uint8_t H_SCLK = 47; 
    static constexpr uint8_t DRDY = 35; 
    static constexpr uint8_t ADS_Cs = 36; 
    static constexpr uint8_t H_MOSI = 34; 
    static constexpr uint8_t ADS_Clk =  37; 

    static constexpr uint8_t TC0_Cs = 48;
    static constexpr uint8_t TCO_Fault = 21;

    // GPIO Breakout
    static constexpr uint8_t GPIO1 = 1; 
    static constexpr uint8_t GPIO2 = 2; 
    static constexpr uint8_t GPIO4 = 4; 
    static constexpr uint8_t GPIO5 = 5; 

    // MISC
    static constexpr uint8_t Abort = 1;
    static constexpr uint8_t Turbine = 2;

    //I2C
    static constexpr uint8_t _SCL = 6;
    static constexpr uint8_t _SDA = 7;


   
};


// v1 Pins
// namespace PinMap{

    
//     // CAN
//     static constexpr uint8_t RxCan = 1; 
//     static constexpr uint8_t TxCan = 2; 
    
//     // SD
//     static constexpr uint8_t SdDet = 4;
//     static constexpr uint8_t SdEN = 5;
//     static constexpr uint8_t SdCs = 6;
//     static constexpr uint8_t V_MOSI = 7;
//     static constexpr uint8_t V_SCLK = 8;
//     static constexpr uint8_t V_MISO = 9;

//     // Servo
//     static constexpr uint8_t ServoPWM1 = 11; 
//     static constexpr uint8_t ServoPWM2 = 10; 
//     static constexpr uint8_t ServoVLog = 12; 

//     // Pyro
//     static constexpr uint8_t PyroIMon = 13;
//     static constexpr uint8_t PyroCont = 14;
//     static constexpr uint8_t PyroNuke = 15;
//     static constexpr uint8_t FuseCont = 16;

//     // LED
//     static constexpr uint8_t LED = 26;

//     // ADS
//     static constexpr uint8_t H_MISO = 33;
//     static constexpr uint8_t H_SCLK = 34; 
//     static constexpr uint8_t DRDY = 35; 
//     static constexpr uint8_t ADS_Cs = 36; 
//     static constexpr uint8_t H_MOSI = 47; 
//     static constexpr uint8_t ADS_Clk =  48; 

//     // GPIO Breakout
//     static constexpr uint8_t GPIO37 = 37; 
//     static constexpr uint8_t GPIO38 = 38; 
//     static constexpr uint8_t GPIO39 = 39; 
//     static constexpr uint8_t GPIO40 = 40; 
//     static constexpr uint8_t GPIO41 = 41; 
//     static constexpr uint8_t GPIO42 = 42; 

//     // MISC
//     static constexpr uint8_t Abort = 40;
//     static constexpr uint8_t Turbine = 41;


   
// };

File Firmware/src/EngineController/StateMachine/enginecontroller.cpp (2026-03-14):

#include "enginecontroller.h"
#include <math.h>
#include <Arduino.h>

#include <libriccore/commands/commandhandler.h>
#include <libriccore/riccorelogging.h>

#include "Deployment/PCA9534.h"
#include "Deployment/PCA9534Gpio.h"


#include "Default.h"
#include "Armed.h"
#include "Ignition.h"
#include "Controlled.h"
#include "Shutdown.h"
#include "Debug.h"

#include "EngineController/Control/throttle.h"

 

EngineController::EngineController(RnpNetworkManager& networkmanager, SensorHandler& sensorHandler, PCA9534& pyroPinExpander):
                    NRCRemoteActuatorBase(networkmanager),
                    _networkmanager(networkmanager),  
                    _sensorHandler(sensorHandler),
                    OxMain(LocalPWM(PinMap::ServoPWM1), networkmanager,"OxMain"),
                    OxMainAdapter(0,OxMain,[](const std::string& msg){RicCoreLogging::log<RicCoreLoggingConfig::LOGGERS::SYS>(msg);}),
                    FuelMain(LocalPWM(PinMap::ServoPWM2),networkmanager,"FuelMain"),
                    FuelMainAdapter(0,FuelMain,[](const std::string& msg){RicCoreLogging::log<RicCoreLoggingConfig::LOGGERS::SYS>(msg);}),
                    Pyro(ArduinoGpio(PinMap::PyroNuke), PCA9534Gpio(pyroPinExpander,PinMap::PyroCont), _networkmanager),
                    PyroAdapter(0,Pyro,[](const std::string& msg){RicCoreLogging::log<RicCoreLoggingConfig::LOGGERS::SYS>(msg);})

{}; 


void EngineController::setup()
{

    OxMain.setup();
    FuelMain.setup();
    Pyro.setup();

    serviceSetup();

     // Abort GPIO
     pinMode(PinMap::Abort,INPUT_PULLDOWN);

    _engineStateMachine.initalize(std::make_unique<Default>(m_DefaultStateParams, *this));

}

void EngineController::update()
{   
    _value = _engineStatus.getStatus();
    _engineStateMachine.update();


};

void EngineController::arm_base(int32_t arg){


    if ( _engineStateMachine.getCurrentStateID() == EC_FLAGS::State_Default){

    PyroAdapter.arm(arg);
    OxMainAdapter.arm(arg);
    FuelMainAdapter.arm(arg);

    if (PyroAdapter.getState().flagSet(LIBRRC::COMPONENT_STATUS_FLAGS::NOMINAL)&& 
        OxMainAdapter.getState().flagSet(LIBRRC::COMPONENT_STATUS_FLAGS::NOMINAL)&&
        FuelMainAdapter.getState().flagSet(LIBRRC::COMPONENT_STATUS_FLAGS::NOMINAL))
            {

                NRCRemoteActuatorBase::arm_base(arg);

                if (this->_state.flagSet(LIBRRC::COMPONENT_STATUS_FLAGS::NOMINAL))
                
                _engineStateMachine.changeState(std::make_unique<Armed>(m_DefaultStateParams, _networkmanager, *this));

            }

    }
    else {

        PyroAdapter.disarm();
        OxMainAdapter.disarm();
        FuelMainAdapter.disarm();
    }

    

}


void EngineController::disarm_base(){

    PyroAdapter.disarm();
    OxMainAdapter.disarm();
    FuelMainAdapter.disarm();

    NRCRemoteActuatorBase::disarm_base();

    _engineStateMachine.initalize(std::make_unique<Default>(m_DefaultStateParams, *this));



}

uint32_t EngineController::getOxAngle()
{
    return OxMain.getValue();
}

uint32_t EngineController::getFuelAngle()
{
    return FuelMain.getValue();
}

float EngineController::getOF()
{
    return m_currOF;
}

float EngineController::getFuelCalc(){

    return m_fuelcalc;
}


void EngineController::serviceSetup(){

    _networkmanager.registerService(OxMainservice,OxMain.getThisNetworkCallback());
    _networkmanager.registerService(FuelMainservice,FuelMain.getThisNetworkCallback());
    _networkmanager.registerService(Pyroservice,Pyro.getThisNetworkCallback());


}

void EngineController::unregisterServices(){

    _networkmanager.unregisterService(OxMainservice);
    _networkmanager.unregisterService(FuelMainservice);
    _networkmanager.unregisterService(Pyroservice);


}

void EngineController::execute_base(int32_t arg)
{

    switch(arg)
    {
        case 1:
        {   
             if (!_engineStatus.flagSet(EC_FLAGS::ARMED))
        {
            break;
        }
            // Ignition
            _engineStateMachine.changeState(std::make_unique<Ignition>(m_DefaultStateParams, _networkmanager, *this));

            break;

        }

        case 2:
        {
            // Shutdown
            _engineStateMachine.changeState(std::make_unique<Shutdown>(m_DefaultStateParams, _networkmanager, *this));

            break;  

        }

        case 3:
        {
            // Debug
            _engineStateMachine.changeState(std::make_unique<Debug>(m_DefaultStateParams, _networkmanager, *this));
            break;

        }

        case 4:
        {
            // Enter Default from Debug

            if(!_engineStatus.flagSet(EC_FLAGS::DEBUG))
            {
                break;
            }

             // Default
            _engineStateMachine.changeState(std::make_unique<Default>(m_DefaultStateParams, *this));

            break;


        }



    }

}

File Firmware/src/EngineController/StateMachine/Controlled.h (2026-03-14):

#pragma once

#include <memory>

#include <libriccore/fsm/state.h>
#include <libriccore/systemstatus/systemstatus.h>
#include <libriccore/commands/commandhandler.h>

#include "Config/systemflags_config.h"
#include "Config/types.h"
#include "enginetypes.h"
#include "enginecontroller.h"

#include "EngineController/Control/throttle.h"
#include "EngineController/Control/OF.h"

#include "EngineController/Control/lut.h"


class Controlled: public Types::EngineTypes ::State_t
{
    public:

    Controlled(Engine::DefaultStateInit& DefaultInitParams, RnpNetworkManager& networkmanager, EngineController& Engine);

    void initialize() override;

    Types::EngineTypes::State_ptr_t update() override;

    void exit() override;


    private:

    Engine::DefaultStateInit& m_DefaultInitParams;
    RnpNetworkManager& _networkmanager;
    EngineController& _engine;

    Types::LocalServoAdapter_t& _OxMainAdapter;
    Types::LocalServoAdapter_t& _FuelMainAdapter;

   
    // Sensor params
    float m_Pc;
    static constexpr uint16_t m_maxPc = 25;

    float m_POx; //Ox injector pressure
    float m_PF; //Fuel injector pressure


////////////////////////////

    // Simple Engine

        uint64_t m_Controlled_duration = 60000; //Duration of the controlled burn (ms)
        uint64_t m_Controlled_Command_time;

        std::vector<float> time_array = {0,100,static_cast<float>(m_Controlled_duration)}; //Float type to be compatible with LuT and Interp template
        std::vector<float> m_OxAngle = {0,95,95};
        std::vector<float> m_FuelAngle = {0,100,100};

    // OX / Fuel Lead timing

        float m_OxDelay = 0; //Ox Valve opening delay (ms)
        float m_FuelDelay = 0; //Fuel Valve opening delay (ms)

    // Valve Limits in the Controlled state

    //Max
    float m_OxAngleLim = 95; 
    float m_FuelAngleLim = 100;

    //Min
    float m_throttleOx_min = 35; 
    float m_throttleFuel_min = 35;


////////////////////////////

    uint8_t m_timeIndex = 0;

    LuT<float,LinearInterp<float>> m_OxAngleLuT;
    LuT<float,LinearInterp<float>> m_FuelAngleLuT;

    float  _nextOxAngle;
    float  _nextFuelAngle;

    float m_Ox_FF;
    float m_Fuel_FF;

    float m_OxPercent = 0.0;
    float m_FuelPercent = 0.0;

    float m_FuelExtra = 0.0;


    // Throttle Params

    float m_OxThrottleRange;
    float m_FuelThrottleRange;

    void updateThrottle();
    void updateOF();

    Throttle m_throttle;
    OF m_OF;

   

};

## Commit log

2023-11-11 Initial template
    [EngineController.kicad_pcb, EngineController.kicad_sch, can.kicad_sch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]
2023-11-11 Engine Controller Board: Added in Buck
    Added in buck for chad and modified resistors to have output of 7.4V and 6V instead of 8.4V
    [EngineController.kicad_sch, buckC.kicad_sch, buckCkicad_sch.kicad_sch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]
2023-11-18 Xavier: Updated Engine Controller
    Added in the actuators
    [EngineController.kicad_sch, actuators.kicad_sch]
2023-11-21 Engine Controller: Added in ads and pressure sensor
    Circuit for both 5v and 10v
    [EngineController.kicad_sch, actuators.kicad_sch, buckCkicad_sch.kicad_sch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]
2024-01-23 Completed schematics
    [EngineController.kicad_pcb, EngineController.kicad_sch, actuators.kicad_sch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]
2024-02-06 Xavier: Modified ADS board
    Pressure Sensor ADS board reduced to ADS131M03 with 3 channels for the 3 pressure sensors
    [boosts_sch.kicad_sch, pressure_sensor_sch.kicad_sch]
2024-03-09 Finished schematic
    [EngineController.kicad_sch, Pyro.kicad_sch, actuators.kicad_sch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]
2024-03-09 Forgot Pyro
    [EngineController.kicad_sch, Pyro.kicad_sch]
2024-03-10 forgot sd card and added ads chip
    [EngineController.kicad_pcb, EngineController.kicad_sch]
2024-03-16 Schematic done, components layed out, sensors wired up
    [EngineController.kicad_pcb, EngineController.kicad_sch, Pyro.kicad_sch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]
2024-03-17 Wired up more stuff
    [EngineController.kicad_pcb, EngineController.kicad_sch, pressure_sensor_sch.kicad_sch]
2024-03-17 All wired up
    [EngineController.kicad_sch]
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2024-03-30 More Based
    [Pyro.kicad_sch, Ricardo-Stark.kicad_sch, actuators.kicad_sch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]
2024-03-30 Last commit wasnt based enough, forgot analogue ground isolation
    [Ricardo-Stark.kicad_pcb]
2024-03-31 Lol pyro buck out was shorting straight to ground
    [Pyro.kicad_sch, buckCkicad_sch.kicad_sch]
2024-03-31 added pyro buck caps
    [Pyro.kicad_sch]
2024-04-03 changed led resistances
    [Ricardo-Stark.kicad_sch]
2024-04-14 Most Review 1 changes made
    [Pyro.kicad_sch, Ricardo-Stark.kicad_sch, boosts_sch.kicad_sch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]
2024-04-19 Review 1 Changes Complete
    [Pyro.kicad_sch, Ricardo-Stark.kicad_sch, boosts_sch.kicad_sch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]
2024-04-21 Fixed USB tracks
    [Ricardo-Stark.kicad_sch]
2024-05-14 Take 3
    [Pyro.kicad_sch, Ricardo-Stark.kicad_sch, boosts_sch.kicad_sch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]
2024-05-15 Sized sensor resistors and more routing
    [Pyro.kicad_sch, Ricardo-Stark.kicad_pcb, Ricardo-Stark.kicad_sch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]
2024-05-20 added silkscreen
    [microSD.kicad_sch]
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2024-05-30 review changes
    [Pyro.kicad_sch, Ricardo-Stark.kicad_sch, actuators.kicad_sch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]
2024-06-01 5v breakout
    [Ricardo-Stark.kicad_sch, actuators.kicad_sch]
2024-06-06 saved leds from blowing
    [Ricardo-Stark.kicad_sch]
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2024-07-17 artem big brain moment
    [Pyro.kicad_sch]
2024-07-25 reshuffled layout
    [Ricardo-Stark.kicad_sch, actuators.kicad_sch, pressure_sensor_sch.kicad_sch]
2024-07-25 Added sensors
    [pressure_sensor_sch.kicad_sch]
2024-07-28 more changes
    [Pyro.kicad_sch, Ricardo-Stark.kicad_sch, actuators.kicad_sch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]
2024-07-30 added 30V input caps
    [Pyro.kicad_sch, buckCkicad_sch.kicad_sch]
2024-08-01 changed boost out
    [boosts_sch.kicad_sch]
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2024-08-04 changed sd mosfet footprint
    [microSD.kicad_sch]
2024-08-04 review 3 changes
    [Ricardo-Stark.kicad_sch, pressure_sensor_sch.kicad_sch]
2024-08-04 tcmt1109 instead of ltv
    [Pyro.kicad_sch, boosts_sch.kicad_sch]
2024-08-07 Andrei review changes
    [boosts_sch.kicad_sch, buckCkicad_sch.kicad_sch]
2024-08-08 fixed sd mosfet footprint
    [bom.csv, designators.csv, positions.csv]
2024-08-12 Changed sd card holder
    [Ricardo-Stark.kicad_sch, actuators.kicad_sch, microSD.kicad_sch]
2024-08-12 LDO 5V resistor change
    [boosts_sch.kicad_sch]
2024-08-16 Fixed sd det
    [bom.csv, designators.csv, microSD.kicad_sch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]
2024-08-24 Added Firmware folder
    [Pyro.kicad_sch, Ricardo-Stark.kicad_sch, Ricardo-Stark.step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]
2024-08-24 Revert "Added Firmware folder"
    This reverts commit db9fcbd56da78149f63fb568c453a94413145aad.
    [Pyro.kicad_sch, Ricardo-Stark.kicad_sch, Ricardo-Stark.step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]
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2024-08-24 Added Firmware
    [Pyro.kicad_sch, Ricardo-Stark.kicad_sch, Ricardo-Stark.step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]
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2024-09-07 Removed circular dependency error
    [enginecontroller.cpp]
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2024-09-13 Ox FF bug fix
    [Controlled.h]
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2024-12-15 Bug fixes + cleanup
    [Controlled.h, OF.h, enginecontroller.cpp]
2025-01-17 updated sensors and other stuff
    [Fuzzzze.kicad_sch, LEDs.kicad_sch, Pyro.kicad_sch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]
2025-02-02 rearranged comps
    [Ricardo-Stark.kicad_sch, boosts_sch.kicad_sch, pressure_sensor_sch.kicad_sch]
2025-03-27 Finished Boosts and Sensors
    [Fuzzzze.kicad_sch, LEDs.kicad_sch, Pyro.kicad_sch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]
2025-03-28 Updated SD card, GPIOs, CAN, Power section
    [Ricardo-Stark.kicad_sch, actuators.kicad_sch, microSD.kicad_sch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]
2025-03-29 Routed Switch and Servo driver subsystems
    [Fuzzzze.kicad_sch, LEDs.kicad_sch, Ricardo-Stark.kicad_sch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]
2025-03-31 Added actuators and I2C bus
    [LEDs.kicad_sch, Ricardo-Stark.kicad_sch, buckCkicad_sch.kicad_sch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]
2025-04-03 Almost done
    [LEDs.kicad_sch, Pyro.kicad_sch, Ricardo-Stark.kicad_sch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]
2025-04-05 Fixed all DRC Errors
    [Pyro.kicad_sch, Ricardo-Stark.kicad_sch, usb.kicad_sch]
2025-04-05 Updated Silkcreen and test points
    [Ricardo-Stark.kicad_sch]
2025-04-06 v2 Ready for Review
    [Ricardo-Stark.kicad_sch, boosts_sch.kicad_sch, buckCkicad_sch.kicad_sch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]
2025-04-11 Most Review Changes
    [LEDs.kicad_sch, Pyro.kicad_sch, Ricardo-Stark.kicad_sch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]
2025-04-12 Remaining Review Changes
    [Pyro.kicad_sch, Ricardo-Stark.kicad_sch]
2025-04-12 Forgot switch enable DNP pull up
    [Pyro.kicad_sch]
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2025-04-25 6 layer and production files
    [bom.csv, designators.csv, positions.csv]
2025-05-22 SD Card bug fix
    [system.cpp]
2025-08-30 fixed LocalPWM old API usage
    [enginecontroller.cpp]
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2025-08-31 Linear Interpolation for engine startup ramp + arming bug fix
    [Controlled.h, enginecontroller.cpp]
2025-10-07 Added TC to sensor handler and shortened telem packet
    [Controlled.h, MAX31856.cpp, MAX31856.h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]

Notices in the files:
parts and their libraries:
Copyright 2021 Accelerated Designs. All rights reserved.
